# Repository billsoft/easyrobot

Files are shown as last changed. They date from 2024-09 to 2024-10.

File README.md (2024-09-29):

# easyrobot
简易四足机器人<br>
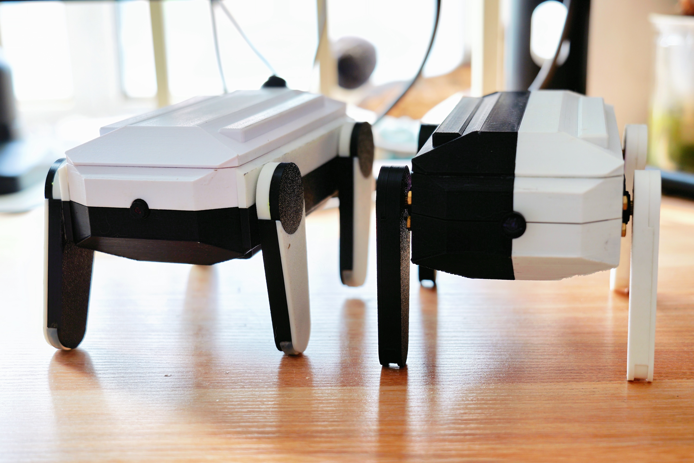
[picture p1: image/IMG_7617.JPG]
安装说明

## 说明
1.esp32文件内为esp32cam程序，用的是micropython，需要烧录文件内固件<br>
2.robot为arduino程序<br>
3.目前电池供电有些问题，舵机或者esp32cam单独供电应该是没什么问题<br>
4.主控可以直接使用arduino uno，不需要用文件里的板子，只是内部用面包板这些会比较乱，但不影响使用。<br>
5.模型可以颜色可自行搭配，模型文件地址<br>
[模型下载地址](https://makerworld.com/zh/models/670436#profileId-598128)<br>
[基本功能演示](https://www.bilibili.com/video/BV1YAxkewE2Q/?vd_source=0b2798e3dbadd3bb799cc7f946455f03)

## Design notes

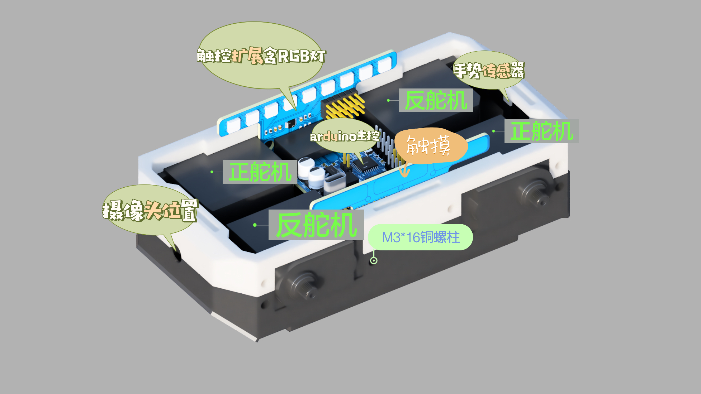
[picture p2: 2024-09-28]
image/舵机安装方式一.JPG

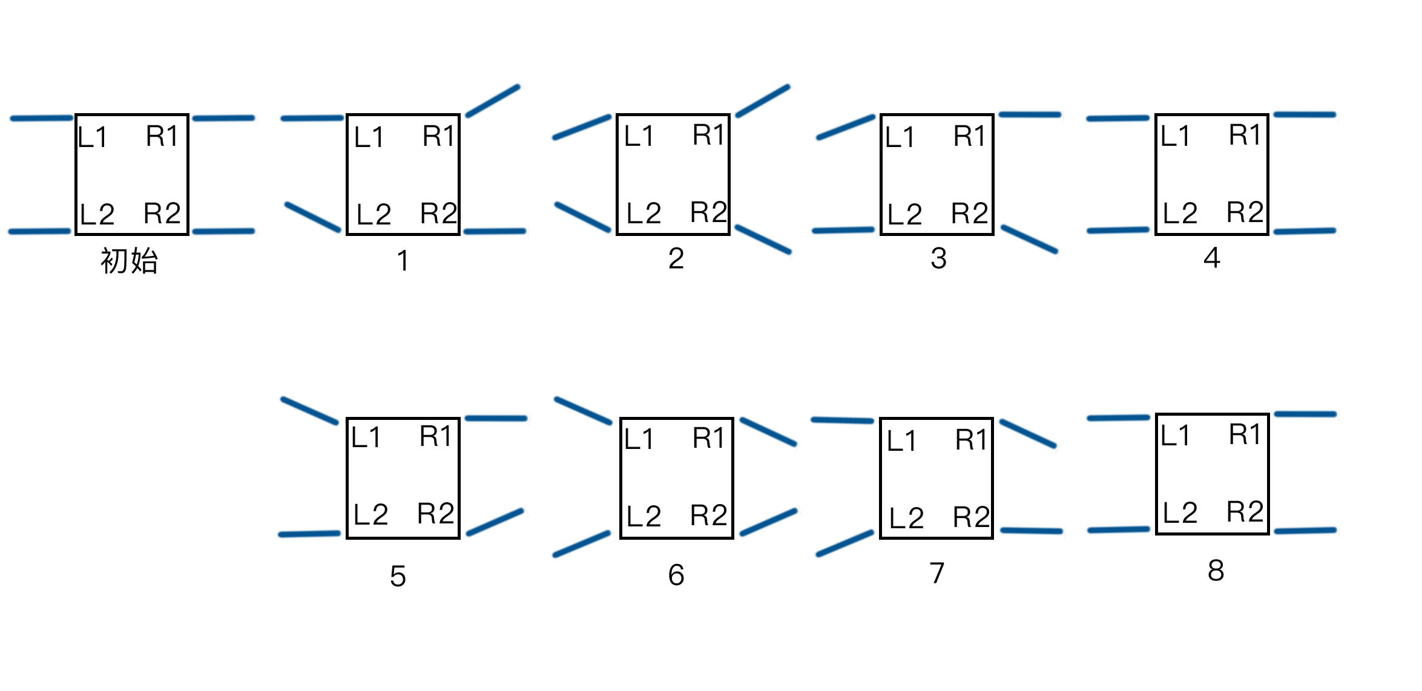
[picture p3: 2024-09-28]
image/前进.png

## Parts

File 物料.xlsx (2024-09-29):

材料 | 数量 | 备注 | 地址
舵机 | 4 | 需正反舵机各两个 | https://item.taobao.com/item.htm?_u=tkvup2c1948&id=570656601445
M3螺丝和螺母 | 16 | 如果不需要触摸可以用普通M4螺丝
ESP32cam
75mm长度ov2640 | 1
paj7602u2手势传感器 | 1 |  | https://detail.tmall.com/item.htm?_u=tkvup2c2cbf&id=620597308205
mpu6050 | 1 | 可自行添加
圆形黄铜圆柱 | 8 | M3*2*5 | https://detail.tmall.com/item.htm?_u=tkvup2cd41a&id=718349103139
锂电池 |  | 7.4V | https://item.taobao.com/item.htm?_u=tkvup2c28f2&id=632089612908
触摸扩展 | 2 | pcb中的金手指插座，直插2*10/20芯不需要触摸可以不用 | https://item.taobao.com/item.htm?_u=tkvup2cc901&id=681917122120
开关 | 1 | 可以选有灯也可以选无灯，自锁开关，也可以换其他便宜开关 | https://item.taobao.com/item.htm?_u=tkvup2c9716&id=563131179256&skuId=5648339879647
磁铁 | 24 | 如果需要药侧板8个磁铁就够了，长度30mm,厚度2mm | https://item.taobao.com/item.htm?_u=tkvup2cba56&id=619686345628

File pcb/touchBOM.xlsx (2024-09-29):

No. | Quantity | Comment | Designator | Footprint | Value | Manufacturer Part | Manufacturer | Supplier Part | Supplier
1 | 3 | 2.54-1x6P直针 | 5V,GND,信号 | HDR-TH_6P-P2.54-V-M-1 |  | 2.54-1x6P直针 | BOOMELE(博穆精密) | C37208 | LCSC
2 | 1 | 100nF | C1 | C0603 | 100nF
3 | 1 | 4.7nF | C2 | C0603 | 4.7nF
4 | 1 | 5pF | C3 | C0603 | 5pF
5 | 9 | XL-5050RGBC-WS2812B | LED1,LED2,LED3,LED4,LED5,LED6,LED7,LED8,LED9 | LED-SMD_4P-L5.0-W5.0-BL_XL-5050RGBC |  | XL-5050RGBC-WS2812B | XINGLIGHT(成兴光) | C2843785 | LCSC
6 | 1 | 20R | R1 | R0603 | 20R
7 | 3 | 1K | R2,R3,R4 | R0603 | 1K
8 | 3 | 10K | R5,R6,R7 | R0603 | 10K
9 | 1 | AS03B(AI03B) | U1 | MSOP-10_L3.0-W3.0-P0.50-LS4.9-BL |  | AS03B(AI03B) | Sam&wing(芯网) | C2681994 | LCSC
10 | 1 | 金手指插座（20p) | 扩展 | 金手指插座（20p)

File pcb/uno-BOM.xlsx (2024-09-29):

No. | Quantity | Comment | Designator | Footprint | Value | Manufacturer Part | Manufacturer | Supplier Part | Supplier
1 | 2 | 22pF | C1,C2 | C0603 | 22pF
2 | 6 | 100nF | C3,C5,C7,C11,C12,C13 | C0603 | 100nF
3 | 3 | 10uF | C4,C6,C8 | C0603 | 10uF
4 | 2 | 100uF | C9,C10 | CAP-SMD_BD6.3-L6.6-W6.6-LS7.2-R-RD | 100uF | RVE1V101M0607 | ROQANG(容强) | C99837 | LCSC
5 | 2 | ZX-XH2.54-2PWT | CN1,CN2 | CONN-SMD_2P-P2.54_MEGASTAR_ZX-XH2.54-2PWT |  | ZX-XH2.54-2PWT | Megastar(兆星) | C7429671 | LCSC
6 | 1 | SS34 | D1 | SMA_L4.4-W2.8-LS5.4-RD |  | SS34 | BORN(伯恩半导体) | C266553 | LCSC
7 | 4 | HDR-M_2.54_1x3P | H1,H2,H3,H4 | HDR-TH_3P-P2.54-V-M |  |  |  | C2937625
8 | 1 | HDR-M_2.54_1x4P | H6 | HDR-TH_4P-P2.54-V-M |  |  |  | C492403
9 | 1 | HDR-M_2.54_2x3 | H9 | HDR-TH_6P-P2.54-V-R2-C3-S2.54_A2541WV-2X3P |  |  |  | C402781
10 | 1 | B-2100S02P-A110 | H10 | HDR-TH_2P-P2.54-V-M-1 |  | B-2100S02P-A110 | Ckmtw(灿科盟) | C124375 | LCSC
11 | 1 | CJ7805 3% | LDO1 | TO-252-2_L6.6-W6.1-P4.58-LS10.1-BR-CW |  | CJ7805 3% | CJ(江苏长电/长晶) | C21706 | LCSC
12 | 2 | LED_0603-R | LED1,LED2 | LED_0603
13 | 1 | 10K | R1 | R0603 | 10K
14 | 4 | 1K | R2,R3,R6,R7 | R0603 | 1K
15 | 2 | 5.1K | R4,R5 | R0603 | 5.1K
16 | 1 | Key_SMD_3x4x2 | SW1 | Key_SMD_3x4x2
17 | 1 | ATMEGA328P-AU | U4 | TQFP-32_L7.0-W7.0-P0.80-LS9.0-BL |  | ATMEGA328P-AU | MICROCHIP(美国微芯) | C14877 | LCSC
18 | 1 | AMS1117-3.3 | U5 | SOT-223-3_L6.5-W3.4-P2.30-LS7.0-BR |  | AMS1117-3.3 | AMS | C6186 | LCSC
19 | 1 | CH340C | U6 | SOP-16_L10.0-W3.9-P1.27-LS6.0-BL |  | CH340C | WCH(南京沁恒) | C84681 | LCSC
20 | 4 | 2.54金手指（20p) | U8,U9,U10,U11 | 金手指（20p)
21 | 1 | HC019-1E1H1A103-0HR | USB1 | USB-C-SMD_HC019-1E1H1A103-0HR |  | HC019-1E1H1A103-0HR | HCTL(华灿天禄) | C2894918 | LCSC
22 | 1 | 16MHz | X1 | CRYSTAL-SMD_4P-L3.2-W2.5-BL-2 | 16MHz | NX3225SA-16MHz-STD-CSR-6 | NDK | C880097 | LCSC

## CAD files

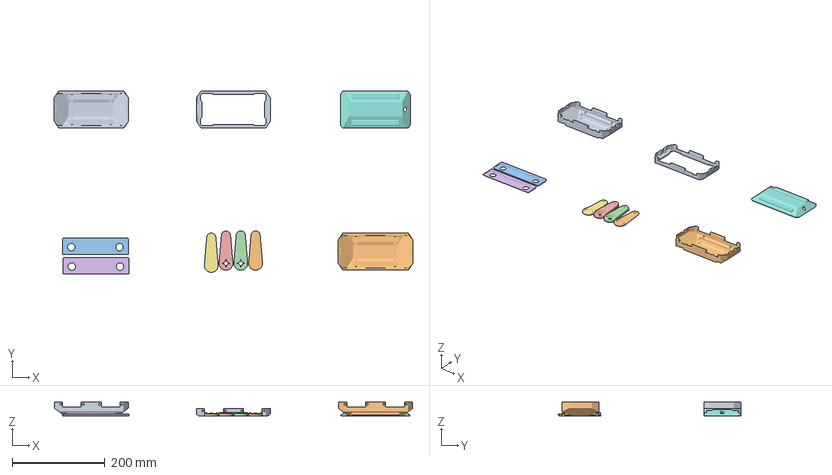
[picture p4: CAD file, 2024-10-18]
pcb/四足mini机器人.3mf
775.9 x 395.4 x 30.0 mm
实体15
腿上.step x 2
四足 v14.step x 2
腿1.step x 2
实体60
实体83
四足2.step

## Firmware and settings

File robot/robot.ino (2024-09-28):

/*
1.动作步态程序可看robotaction.h或者robotactions.h
2.手势识别动作基于paj7620_9gestures 示例修改，具体可看gestures.h
3.RGB和触摸集成到一块扩展，具体引脚参考可以看Rgb_color.h
4.摄像头视频采集和控制采用esp32cam,通过串口通讯接受指令，程序可看相关文件夹
5.mpu6050检测姿态暂时没有写，有想添加的可自行添加
6.纯菜鸟制作，勿喷，有问题可以一起交流，b站: 黄昏近残夜
*/
#include "robotaction.h"
#include "gestures.h"
#include "Rgb_color.h"
#include <SoftwareSerial.h>
#define L1 2
#define R1 3
#define L2 4
#define R2 5
#define camera_led 9
SoftwareSerial mySerial(12,13);
bool touch_turn = false;
bool positive = true,negative = false;
int turn_number = 0;
String esp32_read;
void setup()
{
  // put your setup code here, to run once:
  pinMode(camera_led,OUTPUT);
  set_pin(L1,R1,L2,R2);
  //gestures_init();
  positive_stand_set();
  touch_rgb_init();
  //pinMode(touch,INPUT);
  Serial.begin(9600);
  mySerial.begin(9600);
}

void loop()
{
  if (mySerial.available())
  {
    esp32_read = mySerial.readString();
    Serial.println(esp32_read);
    if (esp32_read == "Camera ready")
    {
      for (int i = 0; i <= 10; i++)
      {
        digitalWrite(camera_led, HIGH);
        delay(200);
        digitalWrite(camera_led, LOW);
        delay(200);
      }
    }
    if (esp32_read == "turn")
    {
      turn_number ++;
      if (turn_number % 2 == 1)
      {
        positive = false;
        do_flip_positive();
      }
      else
      {
        positive = true;
        do_flip_negative();
      }
      negative = !positive;
      Serial.println(turn_number % 2);
      delay(500);
    }

    if (positive)
    { 
      //do_flip_positive();
      if (esp32_read == "go")
      {
        for (int i = 0; i <= 3; i++)
        {
          positive_go();
        }
      }
      else if (esp32_read == "back")
      {
        for (int i = 0; i <=3; i++)
        {
          positive_back();
        }
      }
      else if (esp32_read == "left")
      {
        for (int i = 0; i <=2; i++)
        {
          positive_left();
        }
      }
      else if (esp32_read == "right")
      {
        for (int i = 0; i <=2; i++)
        {
          positive_right();
        }
      }
    }
    if (negative)
    { 
      if (esp32_read == "go")
      {
        for (int i = 0; i <= 3; i++)
        {
          negative_go();
        }
      }
      else if (esp32_read == "back")
      {
        for (int i = 0; i <= 3; i++)
        {
          negative_back();
        }
      }
      else if (esp32_read == "left")
      {
        for (int i = 0; i <= 2; i++)
        {
          negative_left();
        }
      }
      else if (esp32_read == "right")
      {
        for (int i = 0; i <= 2; i++)
        {
          negative_right();
        }
      }
    }
  }
  else 
  {
    touch_rgb_control();
  }
  delay(200);

  /*以下程序是手势识别*/
  /*
  String result_rv = result_gesture();
  //Serial.println(result_rv);
  if (result_rv == "forward")
  {
    Serial.println("向前");
    do_flip_positive();

    for (int i=0;i<=5;i++)
    {
      negative_back();
    }
  }
  
  else if (result_rv == "backward")
  {
    Serial.println("向后");
    for(int i=0;i<=2;i++)
    {
      positive_back();
    }
  }
  /*
  else if (result_rv == "left")
  {
    Serial.println("向左");
    for (int i=0;i<=2;i++)
    {
      posivite_right();
    }
  }
  else if (result_rv == "right")
  {
    Serial.println("向右");
    for (int i=0;i<=2;i++)
    {
      posivite_left();
    }
  }
  else if (result_rv == "up")
  {
    Serial.println("向上");
    positive_stand_set();
  }
  else if (result_rv == "down")
  {
    Serial.println("向下");
    positive_get_down();
  }

  else if (result_rv == "wave")
  {
    Serial.println("挥手");
    for(int i=0;i<=2;i++)
    {
      positive_wave();
    }
    positive_stand_set();
  }
  */
}

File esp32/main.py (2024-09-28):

'''
访问网站端口为5000,程序打印出ip地址后，在ip地址加上端口即可访问
如 192.168.31.233:5000
microdot.py和asynic文件夹放入到esp32根目录下
'''
from microdot import Microdot,send_file
import time,network
import camera
from machine import reset,UART
camera_flip = False
'''
初始化摄像头
'''
try:
    camera.init(0, format=camera.JPEG, fb_location=camera.PSRAM)
except OSError:
    camera.deinit()
    camera.init(0, format=camera.JPEG, fb_location=camera.PSRAM)
camera.flip(camera_flip)
#camera.framesize(camera.FRAME_QVGA)
camera.quality(20) #设置摄像头质量，10为最高
print("Camera ready")
uart1 = UART(1,baudrate = 9600,tx = 12,rx = 13)
uart1.write("Camera ready") # 初始化成功发送至机器人
'''
连接网络
'''
def do_connect():
    wlan = network.WLAN(network.STA_IF)
    wlan.active(True)
    if not wlan.isconnected():
        print('正在连接网络...')
        wlan.connect('填入账号','填入密码')
    print('network config:', wlan.ifconfig())
    return wlan.ifconfig()[0]
#time.sleep(5)  延时的作用是防止下次网络连接报错，可不用
do_connect()
app = Microdot()
'''
以下网页接受代码参考B站Up主 red润老师
Microdot()框架的使用可以在https://juejin.cn/post/7246340035065249829#heading-6 查看
目前Microdot已更新，相对于介绍内容更强大
'''
@app.route('/')
async def index(request):
    return send_file('/index.html')
@app.get('/go')
async def index(request):
    uart1.write("go")
    print("go")
    return "前进"
@app.get('/back')
async def index(request):
    uart1.write("back")
    print("back")
    return "后退"
@app.get('/left')
async def index(request):
    uart1.write("left")
    print("left")
    return "左转"
@app.get('/right')
async def index(request):
    uart1.write("right")
    print("right")
    return "右转"
@app.get('/turn')
async def index(request):
    global camera_flip
    uart1.write("turn")
    camera_flip = not camera_flip
    camera.flip(camera_flip)
    print("turn")
    return "翻转"
'''
网页图传
代码来源于B站up主"F的工作室"老师
'''
@app.route('/video_feed')
async def video_feed(request):
    def stream():
        yield b'--frame\r\n'
        while True:
            frame = camera.capture()
            yield b'Content-Type: image/jpeg\r\n\r\n' + frame + \
                b'\r\n--frame\r\n'

    return stream(), 200, {'Content-Type':
                           'multipart/x-mixed-replace; boundary=frame'}



app.run()

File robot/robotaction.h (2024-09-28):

/*
1.前进后退等动作分解，可对应动作图例文件夹内图片分析
2.步态动作参考b站up主石桥北老师，地址：
https://www.bilibili.com/video/BV1yH4y1U7Zo/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
3.使用舵机为270度舵机，某宝不算贵，14元一个（地址可看文件夹内的物料清单）
4.需要舵机方向两正两反，目的是保持转动方向一致
5.程序稍微长，可以使用优化版robotactions.h（暂未验证，此程序舵机安装为同侧正反相同，即正正反反，安装方式见安装示例图）
6.此程序为舵机安装为异向，即正反反正，安装方式见安装示例图
*/
#include <Servo.h>
Servo myservo_L1;
Servo myservo_R1;
Servo myservo_L2;
Servo myservo_R2;
int L1_init_pt = 40;
int R1_init_pt = 48;
int L2_init_pt = 45;
int R2_init_pt = 55;
int L1_init_nt = 220;
int R1_init_nt = 228;
int L2_init_nt = 225;
int R2_init_nt = 235;
int angle = 20;
int servo_270(int x) //将180度舵机转为270度
{
  int angle = map(x,0,270,0,180);
  return angle;
}
void set_pin(int L1_Pin,int R1_Pin,int L2_pin,int R2_Pin)
{
  myservo_L1.attach(L1_Pin);
  myservo_R1.attach(R1_Pin);
  myservo_L2.attach(L2_pin);
  myservo_R2.attach(R2_Pin);
}  
//初使站立状态
//具体数值需要根据安装调整，270度的舵机因为上下翻转
//所以最开始状态设置在45度左右

void positive_stand_set()//正向站立初始化角度
{ 

  myservo_L1.write(servo_270(L1_init_pt));
  myservo_R1.write(servo_270(R1_init_pt));
  myservo_L2.write(servo_270(L2_init_pt));
  myservo_R2.write(servo_270(R2_init_pt));

}
void negative_stand_set()//反向站立初始化角度
{
  myservo_L1.write(servo_270(L1_init_nt));
  myservo_R1.write(servo_270(R1_init_nt));
  myservo_L2.write(servo_270(L2_init_nt));
  myservo_R2.write(servo_270(R2_init_nt));
}

void positive_go()//正向站立向前行走
{
  //L1 40,R1 48,L2 45,R2 55
  //可以减少延时增加速度
  // 动作 1-2
  myservo_R1.write(servo_270(R1_init_pt + angle));
  delay(150);
  myservo_L2.write(servo_270(L2_init_pt - angle));
  delay(150);
  myservo_L1.write(servo_270(L1_init_pt - angle));
  delay(150);
  myservo_R2.write(servo_270(R2_init_pt + angle));
  delay(150);
 
  // 动作 3-4
  myservo_R1.write(servo_270(R1_init_pt));
  delay(150);
  myservo_L2.write(servo_270(L2_init_pt));
  delay(150); 
  myservo_L1.write(servo_270(L1_init_pt));
  delay(150);
  myservo_R2.write(servo_270(R2_init_pt));
  delay(150);
  // 动作 5-6
  myservo_L1.write(servo_270(L1_init_pt + angle));
  delay(150);
  myservo_R2.write(servo_270(R2_init_pt - angle));
  delay(150);
  myservo_R1.write(servo_270(R1_init_pt - angle));
  delay(50);
  myservo_L2.write(servo_270(L2_init_pt + angle));
  // 动作 7-8
  myservo_L1.write(servo_270(L1_init_pt));
  delay(150);
  myservo_R2.write(servo_270(R2_init_pt));
  delay(150);
  myservo_R1.write(servo_270(R1_init_pt));
  delay(150);
  myservo_L2.write(servo_270(L2_init_pt));
  delay(150);

}
void positive_back()//正向倒走
{
  //初始L1 40,R1 48,L2 45,R2 55
  //动作 1-2
  myservo_L2.write(servo_270(L2_init_pt + angle));
  delay(150);
  myservo_R1.write(servo_270(R1_init_pt - angle));
  delay(150);
  myservo_R2.write(servo_270(R2_init_pt - angle));
  delay(150);
  myservo_L1.write(servo_270(L1_init_pt + angle));
  delay(150);
  //动作 3-4
  myservo_L2.write(servo_270(L2_init_pt));
  delay(150);
  myservo_R1.write(servo_270(R1_init_pt));
  delay(150);
  myservo_R2.write(servo_270(R2_init_pt));
  delay(150);
  myservo_L1.write(servo_270(L1_init_pt));
  delay(150);
  //动作 5-6
  myservo_R2.write(servo_270(R2_init_pt + angle));
  delay(150);
  myservo_L1.write(servo_270(L1_init_pt - angle));
  delay(150);
  myservo_L2.write(servo_270(L2_init_pt - angle));
  delay(150);
  myservo_R1.write(servo_270(R1_init_pt - angle));
  delay(150);
  //动作 7-8
  myservo_R2.write(servo_270(R2_init_pt));
  delay(150);
  myservo_L1.write(servo_270(L1_init_pt));
  delay(150);
  myservo_L2.write(servo_270(L2_init_pt));
  delay(150);
  myservo_R1.write(servo_270(R1_init_pt));
  delay(150);
}
void negative_go()//反向站立向前行走
{
  //初始L1 220，R1 228，L2 225,R2 235
  //动作 1-2
  myservo_R1.write(servo_270(R1_init_nt - angle));
  delay(150);
  myservo_L2.write(servo_270(L2_init_nt + angle));
  delay(150);
  myservo_L1.write(servo_270(L1_init_nt + angle));
  delay(150);
  myservo_R2.write(servo_270(R2_init_nt - angle));
  delay(150);

  //动作 3-4
  myservo_R1.write(servo_270(R1_init_nt));
  delay(150);
  myservo_L2.write(servo_270(L2_init_nt));
  delay(150);
  myservo_L1.write(servo_270(L1_init_nt));
  delay(150);
  myservo_R2.write(servo_270(R2_init_nt));
  delay(150);

  //动作 5-6
  myservo_L1.write(servo_270(L1_init_nt - angle));
  delay(150);
  myservo_R2.write(servo_270(R2_init_nt + angle));
  delay(150);
  myservo_R1.write(servo_270(R1_init_nt + angle));
  delay(150);
  myservo_L2.write(servo_270(L2_init_nt - angle));
  delay(150);

  //动作 7-8
  myservo_L1.write(servo_270(R1_init_nt));
  delay(150);
  myservo_R2.write(servo_270(R2_init_nt));
  delay(150);
  myservo_R1.write(servo_270(R1_init_nt));
  delay(150);
  myservo_L2.write(servo_270(L2_init_nt));
  delay(150);
}
void negative_back()//反向倒走
{
  //初始L1 220，R1 228，L2 225,R2 235
  //动作 1-2
  myservo_L2.write(servo_270(L2_init_nt - angle));
  delay(150);
  myservo_R1.write(servo_270(R1_init_nt + angle));
  delay(150);
  myservo_R2.write(servo_270(R2_init_nt + angle));
  delay(150);
  myservo_L1.write(servo_270(L1_init_nt - angle));
  delay(150);
  //动作 3-4
  myservo_L2.write(servo_270(L2_init_nt));
  delay(150);
  myservo_R1.write(servo_270(R1_init_nt));
  delay(150);
  myservo_R2.write(servo_270(R2_init_nt));
  delay(150);
  myservo_L1.write(servo_270(L1_init_nt));
  delay(150);
  //动作 5-6
  myservo_R2.write(servo_270(R2_init_nt - angle));
  delay(150);
  myservo_L1.write(servo_270(L1_init_nt + angle));
  delay(150);
  myservo_L2.write(servo_270(L2_init_nt + angle));
  delay(150);
  myservo_R1.write(servo_270(R1_init_nt - angle));
  delay(150);
  //动作 7-8
  myservo_R2.write(servo_270(R2_init_nt));
  delay(150);
  myservo_L1.write(servo_270(L1_init_nt));
  delay(150);
  myservo_L2.write(servo_270(L2_init_nt));
  delay(150);
  myservo_R1.write(servo_270(R1_init_nt));
}
void positive_get_down() //正向站立时趴下
{
  myservo_L1.write(servo_270(90));
  myservo_R1.write(servo_270(98));
  delay(150);
  myservo_L2.write(servo_270(95));
  myservo_R2.write(servo_270(105));
}
void negative_get_down() //反向站立时趴下
{
  myservo_L1.write(servo_270(180));
  myservo_R1.write(servo_270(188));
  delay(150);
  myservo_L2.write(servo_270(185));
  myservo_R2.write(servo_270(195)); 
}
void do_flip_positive()//正向站立时翻跟头
{
  positive_stand_set();
  delay(100);
  myservo_L1.write(servo_270(0));
  myservo_R1.write(servo_270(8));
  delay(100);
  myservo_L2.write(servo_270(0));
  myservo_R2.write(servo_270(10));
  delay(2000);
  myservo_L2.write(servo_270(260));
  myservo_R2.write(servo_270(270));
  delay(1000);
  myservo_L1.write(servo_270(260));
  myservo_R1.write(servo_270(268));
  delay(1000);
  negative_get_down();
  

}
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
